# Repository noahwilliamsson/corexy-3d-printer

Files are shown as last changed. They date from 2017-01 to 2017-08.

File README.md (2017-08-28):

# Overview

This is my attempt at designing a 3D printer with [CoreXY](http://corexy.com/theory.html) motion.  There's nothing novel about it except all plastic parts were designed in the open source [OpenSCAD](http://www.openscad.org).  So far it has successfully printed a 20mm calibration cube.

The printer has been built around some 2020 aluminium extrusions I had lying around:

- 4x 500mm beams for the frame (X)
- 4x 420mm beams for the frame (Y)
- 4x 360mm beams for the frame (Z)
- 2x 360mm beams for the bed (X)
- 2x 420mm beams for the bed (Y)

For the linear motion, 4x 12x400mm stainless steel rods (X and Y) and 4x 10x400mm (Z axises) have been used together with 8x LM12UU bearings and IGUS DryLin RJMP-01-10 bearings.

The plastic parts were printed in PLA, with some of the load bearing parts printed at 100% infill.

In the current design it requires 4 NEMA17 stepper motors (two for the corexy motion and two to support the bed in the Z direction).

For the extruder and hotend, an [E3D Titan Extruder](https://e3d-online.com/Titan-Extruder) is used with an [E3D v6 HotEnd](https://e3d-online.com/E3D-v6/Full-Kit/v6-1.75mm-Universal).

Electronics wise, it uses an Arduino Mega2560 r3 board and has been tested with both:

- 4x [Big Easy Driver](http://www.schmalzhaus.com/BigEasyDriver/) stepper motor drivers and a custom board with MOSFETs and misc support electronics
- A standard [RAMPS v1.4](http://reprap.org/wiki/RAMPS_1.4) board

The Arduino board runs the [Marlin 1.1.0 RC8](https://github.com/MarlinFirmware/Marlin) firmware with the following settings in `Configuration.h`:

	#define COREXY
	// Travel limits after homing (units are in mm)
	#define X_MAX_POS 290
	#define Y_MAX_POS 275
	#define Z_MAX_POS 205

The Y max value is no longer up-to-date because it was determined when I was using a cantilever design for the bed (single Z axis).  Unfortunately, it wasn't rigid enough and I got some 5mm flex at the far end.  I've since moved on to a dual Z-axis design to support the bed in two places (not reflected in the .scad file).

This is work in progress but here's a quick screenshot from OpenSCAD of the general idea (not all parts are shown).

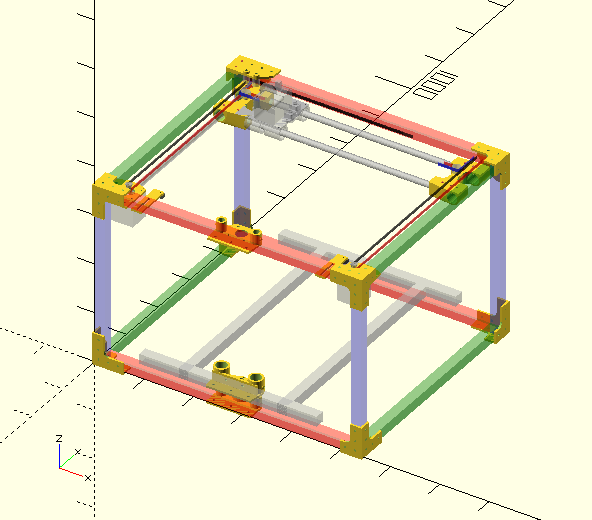
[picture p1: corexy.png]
corexy.scad


# Update 2017

Changed made since the initial commit:

- The horizontal X carriage offered stability but hid the print head so I've opted for a vertical X axis with a new X carriage and new X/Y guide brackets
- The new V2 X carriage is now slightly more modular to make it easier to swap out the print head
- The new V2 X/Y guide brackets are however painful to print properly (use a brim)
- Some parts got slightly rounded corners instead of sharp edges to avoid warping issues
- The X beam length has been reduced to reduce weight of the X axis
- Flexible couplers on the Z axis were replaced with non-flexible ones to reduce lag/flex in the Z axis
- The NEMA17 defs was changed from 43.2mm to 42.3mm (required a re-print of most of the top parts)
- The single, large .scad file has been split up to multiple files

## Imported models

The following STLs were found and downloaded from the internet.

- [BLTouch_extracted.stl](https://www.thingiverse.com/thing:1229934/apps) (CC-BY license)
- [E3D_Titan.stl](https://www.youmagine.com/designs/e3d-titan-extruder-model) (CC-BY-SA license)
- [E3D_V6_1.75mm_Universal_HotEnd_Mockup.stl](https://www.thingiverse.com/thing:341689) (CC-BY license)

# Approximate BOM

Notes:

- All-in-all it's about €1K not including time spent building, waiting, printing and debugging
- Don't cheap out on the hotend, extruder or the heated bed
- While PEI on a heated bed is nice, both PLA and PETG is painless to print on a 4mm float glass bed with 3M Blue Painter's tape (`#2090`)
- Motedis or McMaster-Carr has aluminium beams, steel rods, nuts, washers and bolts for the frame
- China (eBay) has cheaper kits with Arduino+RAMPS 1.4+stepper drivers (€30 in total, saving €50+ vs. buying from E3D)
- The Panucatt Devices _Re-ARM for RAMPS_ board (runs Smoothieware instead of Marlin) is a nice alternative to the Arduino Mega2560 (€40 + shipping)
- I've found the Panucatt Devices _SD6128 Stepper driver_ better able to drive the recent pancake stepper motor E3D offers with their Titan Extruder
- Bearings, misc nuts, washers and bolts can be found on eBay
- Large washers are preferred to spread out the load on plastic parts
- M4 bolts are used around the frame (approx. 150 bolts, washers and alu beam nuts)
- M3 bolts are used in brackets for steppers, electronics, bed leveling and the print head

| Item | Vendor | Count | Price  | Total EUR |
|---|---|---|---|---|
| [Arduino Mega 2560 Compatible Controller Board & USB Cable](https://e3d-online.com/Electrical/Electronics-Boards/Arduino-Mega-2560-Compatible-Board) | E3D Online | 1 | £25 | 28.50 |
| [RAMPS 1.4 - Arduino Mega Pololu Shield](https://e3d-online.com/Electrical/Electronics-Boards/RAMPS-1.4-Arduino-Mega-Pololu-Shield) | E3D Online | 1 | £25 | 28.50 |
| [A4988 Stepper Driver with Heatsink](https://e3d-online.com/A4988-Stepper-Driver-with-Heatsink) | E3D Online | 4 | £6.50  | 29.50 |
| [v6 HotEnd Full Kit - 1.75mm Universal (Direct) (12v)](http://e3d-online.com/E3D-v6/Full-Kit/v6-1.75mm-Universal) (assembled +£12.50) | E3D Online | 1 | £43 | 49.00 |
| [Titan Extruder](https://e3d-online.com/Titan-Extruder)+Mounting bracket+Motor: NEMA17 21N | E3D Online | 1 | £56 | 63.50 |
| [PCB Heated Bed MK2B 12v and 24v](https://e3d-online.com/Mechanical/Print-Surfaces/PCB-Heated-Bed-MK2B-12v-and-24v) | E3D Online | 1 | £12.50 | 13.50 |
| [Borosilicate Glass Beds 214x214x4](https://e3d-online.com/Print-Surfaces/Borosilicate-Bed-200x200) (214x314x4 +£7.00) | E3D Online | 1 | £22 | 25.00 |
| [100k Ohm NTC Thermistor - Semitec](https://e3d-online.com/Electrical/100k-Ohm-NTC-Thermistor-Semitec) | E3D Online | 1 | £3.50  | 4.00 |
| [NEMA17 47N-cm - High Torque Axes Stepper Motor - Wantai](https://e3d-online.com/Electrical/Stepper-Motors/NEMA17-47Ncm) | E3D Online | 4 | £9.30  | 42.00 |
| [GT2 Belt (6mm) (per 100mm)](https://e3d-online.com/Mechanical/Motion/GT2-Belt-6mm) | E3D Online | 24 | £0.35  | 9.50 |
| [GT2 Pulley (16 tooth)](https://e3d-online.com/Mechanical/Motion/GT2-Pulley-16-Tooth) | E3D Online | 2 | £3.50  | 8.00 |
| [Flexible motor coupling 5mm to 8mm](https://e3d-online.com/Mechanical/Motion/Flexible-motor-coupling-5mm-to-8mm) | E3D Online | 2 | £2.50  | 5.65 |
| [40x40x10mm 12v DC Fan](https://e3d-online.com/Electrical/Fans/40x40x10mm-12v-DC-Fan) | E3D Online | 2 | £4.50  | 10.50 |
| [Bulldog Clips x 4](https://e3d-online.com/Mechanical/Fixings/Bulldog%20Clips) | E3D Online | 1 | £0.90  | 1.00 |
| [Compression spring - 20mm x 7.5mm](https://e3d-online.com/Mechanical/Fixings/Compression-spring-20mmx7.5mm-) | E3D Online | 4 | £0.50  | 2.50 |
| [Endstop Microswitches - Omron](https://e3d-online.com/Endstop-Microswitches-Omron) | E3D Online | 5 | £1.50  | 8.50 |
| E3D shipping and VAT (£16+£61) | | 1 | £77 | 87.00 |
| E3D Total | | 1 | £367 | 415.00 |
| | | | | |
| Be Quiet! ATX PSU | | 1 | €60 | 60.00 |
| Filament 1.75mm 1KG spool | | 1 | €30 | 30.00 |
| 8x400mm T8 2mm pitch lead screw plus nut | | 2 | €10 | 20.00 |
| NEMA17 stepper motor vibration dampener | | 2 | €2.5 | 5.00 |
| Misc electrical cables and cable guides | | 1 | €40 | 40.00 |
| Aluminium beams 20x20 (X 4x500mm; Y 6x420mm; Z 6x360mm) | | 1 | €100 | 100.00 |
| Nuts and bolts | | 1 | €150 | 150.00 |
| Stainless steel rods 12x400mm (X and Y guides) | | 4 | €8 | 32.00 |
| Stainless steel rods 8x3600mm (Z guides) | | 4 | €7 | 28.00 |
| Bearing 608 (Z screw bottom) | | 2 | €3 | 6.00 |
| Bearing F624 (X/Y guide bracket) | | 8 | €3 | 24.00 |
| Bearing F695 (corner brackets) | | 16 | €3 | 18.00 |
| Bearing LM12UU (X/Y guide rods) | | 8 | €4 | 32.00 |
| Bearing LM8UU (Z guide rods) | | 4 | €4 | 16.00 |
| Printed parts | | 1 | €50 | 50.00 |
| | | | | |
| Total | | 1 | €1030  | 1030.00 |

# Wiring

RAMPS 1.4 pinout
RAMPS 1.4 wiring

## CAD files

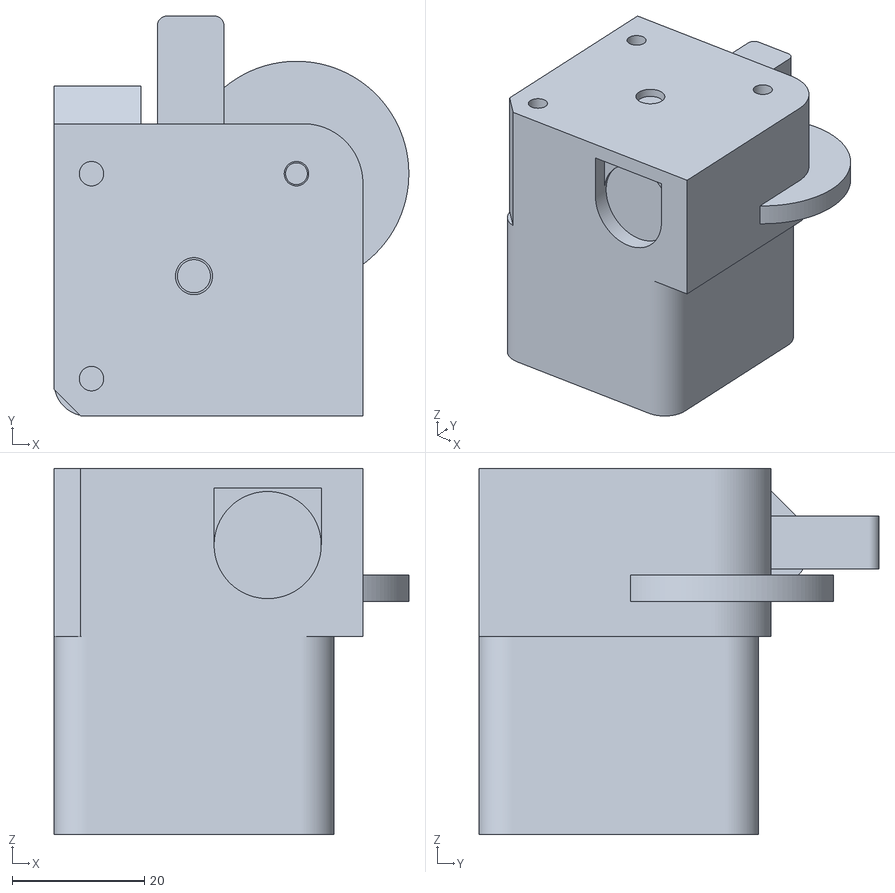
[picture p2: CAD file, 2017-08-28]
E3D_Titan.stl
53.7 x 60.5 x 55.4

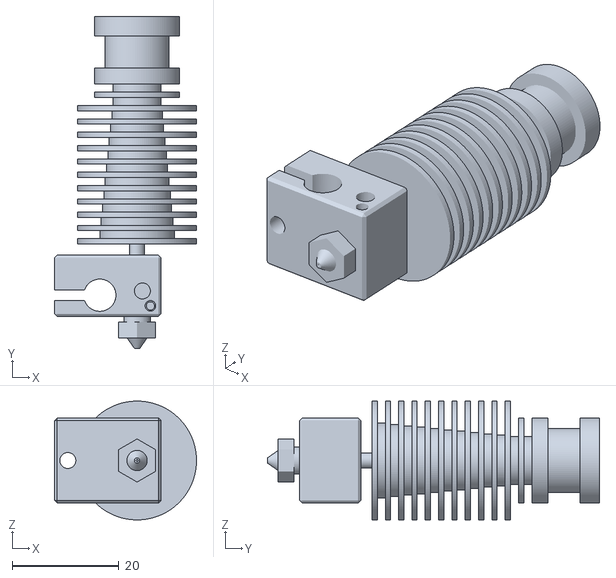
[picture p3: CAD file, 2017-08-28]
E3D_V6_1.75mm_Universal_HotEnd_Mockup.stl
26.6 x 62.3 x 22.3

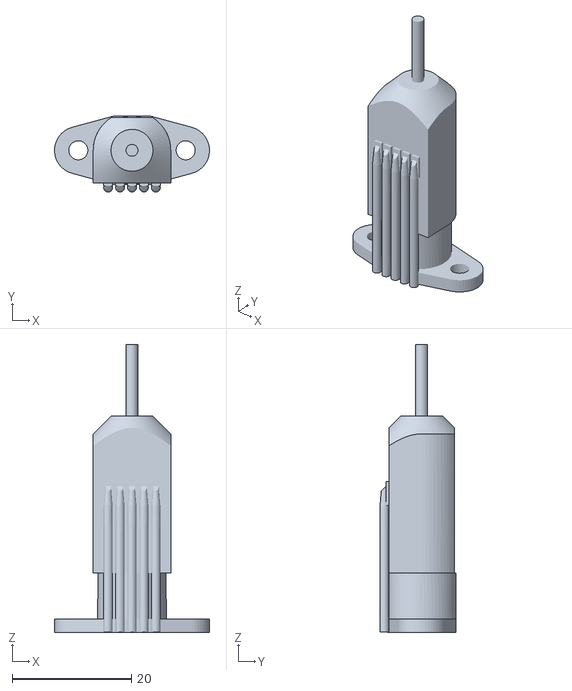
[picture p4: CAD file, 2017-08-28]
BLTouch_extracted.stl
26.0 x 12.8 x 48.3

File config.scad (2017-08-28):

/**
 * CoreXY v2
 * Configuration parameters
 *
 *   -- noah@hack.se, 2016-2017
 */

// Sizes for bearing, screw holes/taps, ..
include <defs.scad>


// Wall thickness
thickness=4;
// Aluminium extrusion size
beamSize=20;

xBeamLength=500;
xRodLength=400;
xBearing=lm12uu;
// XXX: New
xRodLength=400;
xBeamLength=420;
xBearing=lm10uu;

yBeamLength=420;
yRodLength=400;
yBearing=lm10luu;

zBeamLength=360;
zRodLength=300;
zBearing=lm8uu;  // Guide rod
zLeadScrewBearing=B608;
zNut=[8,22,10.5, 8]; // ID, OD (flange), OD (cylinder), mounting hole center-to-center radius

// Bed beams
bedXBeamLength=360;
bedYBeamLength=420;


// Bearings for belt on xy guide bracket
//xyBearing=F625; // 2016
xyBearing=F695; // update 2017
// XY guide bracket clearance from beams
beamClearance=.5;
// Y rod offset from beam, should be > (yBearing[1]/2+thickness)
yRodBeamOffset=13;

// Corner bearings
cornerBearing=F695;

// Distance between X rods (center-to-center)
// Lulzbot, Adapto and other designs use 70mm distances
xRodDistance=70;
// How much to shift X axis up
xRodZShift=5;
// Total width of X rod bracket that is sliding on the Y axis
// Should be at least xRodDistance+2*(xBearing[1]/2+thickness)
xyGuideBracketWidth=99;

xyStepper=NEMA17;
zStepper=NEMA17;
xyPulleySize=9.6;
xyPulleySizeWithBelt=11.6;
xyBeltThickness=1;

xCarriageWidth=70;
xCarriageHeight=xRodDistance+xBearing[1];
xRodMinimumXOffset=beamSize+yRodBeamOffset+yBearing[1]/2;
xRodCalculatedXOffset = beamSize+(xBeamLength-xRodLength)/2;
xGuideLengths=xRodCalculatedXOffset-xRodMinimumXOffset+10+thickness;
xTravel=beamSize+xBeamLength+beamSize-2*(xRodMinimumXOffset+xGuideLengths)-xCarriageWidth;
echo("INFO:",xTravel=xTravel, xRodMinimumXOffset=xRodMinimumXOffset, xRodCalculatedXOffset=xRodCalculatedXOffset, xGuideLengths=xGuideLengths);

yBearingShellDiameter = yBearing[1]+2*thickness < 2*(yRodBeamOffset-beamClearance)? yBearing[1]+2*thickness: 2*(yRodBeamOffset-beamClearance);
echo("Y bearing shell diameter", yBearing[1]+2*thickness, "can be at most", 2*(yRodBeamOffset-beamClearance),"with yRodBeamOffset",yRodBeamOffset,"and beamClearance",beamClearance);

if(yRodBeamOffset <= (yBearing[1]/2+thickness))
    echo("WARNING: yRodBeamOffset too small, need to be at least", (yBearing[1]/2+thickness));
if(xyGuideBracketWidth < xRodDistance+2*(xBearing[1]/2+thickness))
    echo("WARNING: xyGuideBracketWidth too small, need to be at least", xRodDistance+2*(xBearing[1]/2+thickness));


// For the Arduino bracket
board = ArduinoMega2560_Board;
holes = ArduinoMega2560_ReverseHoles;
standoffHeight = 3;

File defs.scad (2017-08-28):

/**
 * CoreXY v2 config
 *
 *   -- noah@hack.se, 2016-2017
 */


/**
 * @section Definitions
 */
// inner diameter, outer diameter, length/height
lm8uu=[8,15,24];    // same as RJ4JP-01-08
lm8luu=[8,15,45];
rjmp0108=[8,16,25]; // RJMP-01-08

lm10uu=[10,19,29];  // same as RJ4JP-01-10
lm10luu=[10,19,55];
rjmp0110=[10,19,29]; // RJMP-01-10

lm12uu=[12,21,30];  // same as  -01-12
lm12luu=[12,21,57];
rjmp0112=[12,22,32]; // RJMP-01-12

// Ball bearings (ID, OD (not considering flange), thickness, flange thickness)
B623=[3,10,5];
B624=[4,13,5];
F624=[4,13,5, 1];
B625=[5,16,5];
F625=[5,16,5, 1];
F695=[5,13,4, 1];
B626=[6,19,6];
B608=[8,22,7];

/**
 * @section Hole configuration
 */
M2tap=1.85;
M3tap=2.85;
M3hole=3.6;
M4tap=3.9;
M4hole=4.6;
M5tap=4.8;
M5hole=5.4;
M5nut=8;
M8tap=7.5;

// X, Y, Height, axle diameter, half distance between two mounting holes, axle length
// Was: NEMA17=[43.2, 43.2, 50, 5, 31/2, 22];
NEMA17=[42.3, 42.3, 50, 5, 31/2, 22];


/**
 * @section Electronics definitions
 */

// https://blog.arduino.cc/2011/01/05/nice-drawings-of-the-arduino-uno-and-mega-2560/
ArduinoMega2560_Board=[101.6,53.4]; // X, Y
ArduinoMega2560_Holes=[
        [14, 2.54],  // bottom left
        [15.24, 50.8], // top left
//        [66.04, 7.62],  // bottom middle,
//        [66.04, 35.56],  // top middle,
        [96.52, 2.54],  // bottom right,
        [90.17, 50.8],  // top right,
];
ArduinoMega2560_ReverseHoles = [
    [11.43, 2.54],
    [86.36, 2.54],
//    [35.56, 17.78],
//    [35.56, 45.72],
    [5.08, 50.8],
    [87.63, 50.8]
];

Pi3_Board=[85,56];
Pi3_Holes=[
    [3.5, 3.5],
    [3.5, 52.5],
    [61.5, 52.5],
    [61.5, 3.5]
];

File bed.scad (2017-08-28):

/**
 * CoreXY v2
 * Modules for the bed
 *
 *   -- noah@hack.se, 2016-2017
 */

// Sizes for bearing, screw holes/taps, ..
include <defs.scad>
// Printer configuration
include <config.scad>

// Modules
use <helpers.scad>


// Print statements
*!bedGripThing();
*!printBedCorners();
*!printBedDistances();

// Print helpers
module printBedCorners() {
    translate([0,0,0]) bedCorner();
    translate([42,0,0]) bedCorner();
    translate([0,42,0]) bedCorner();
    translate([42,42,0]) bedCorner();
}
module printBedDistances() {
    translate([0,0,0]) bedDistance();
    translate([42,0,0]) bedDistance();
    translate([0,42,0]) bedDistance();
    translate([42,42,0]) bedDistance();
}

// To squeeze a plate of 4mm float glass and 4mm cork against a 2020 alu beam
module bedGripThing() {
    distance=28;
    thickness=4;
    difference() {
        union() {
            hull() for(x=[-1,1],y=[-1,1],z=[-1,1])
                translate([(thickness)/2+x*(distance)/2,
                            (2*thickness+distance/2)+y*(2*thickness+distance)/2,
                            5+5*z])
                    sphere(d=1,$fn=6);
        }
        translate([-2*thickness,2*thickness,-.5]) hull() for(x=[-1,1],y=[-1,1],z=[-1,1])
            translate([distance/2+x*distance/2, distance/2+y*distance/2, 5+(5+1)*z])
                sphere(d=1,$fn=6);
    }
}

// Bed leveling screw bracket for Z gantry
module bedCorner() {
    difference() {
        union() {
            cube([beamSize, 6*beamSize/7, thickness]);
            translate([0,5*beamSize/7,0]) cube([beamSize, 4*beamSize/7, thickness]);
            translate([beamSize/4,5*beamSize/7,0]) cube([beamSize/2, 4*beamSize/7, thickness*2]);
            translate([3*beamSize/4, 3*beamSize/3,8]) rotate([0,-90,0]) cylinder(d=12, h=beamSize/2);
        }
        // Mounting holes
        translate([beamSize/2, 2*beamSize/5, -.5]) polyhole(d=M4hole,h=thickness*2+1);
        translate([beamSize+.5, 3*beamSize/3,8]) rotate([0,-90,0]) cylinder(d=M3tap, h=beamSize+1);
    }
}

// Thing for the angled corners on the borosillicate glass
module bedDistance() {
    difference() {
        union() {
            cylinder(d=8,h=thickness);
            rotate(45) translate([-4,-6,0]) cube([8,12,thickness]);
        }
        translate([0,0,-.5]) cylinder(d=M3hole, h=thickness+1);
    }
}

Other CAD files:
corexy-v2.scad
corexy.scad
display.scad
electronics.scad
frame.scad
helpers.scad
xAxis.scad
xyShared.scad
yAxis.scad
zAxis.scad

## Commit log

2017-01-15 Initial import
    [corexy.scad]
2017-08-28 Vertical X axis for V2, approx. BOM, split up scad (WIP)
    [BLTouch_extracted.stl, E3D_Titan.stl, E3D_V6_1.75mm_Universal_HotEnd_Mockup.stl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]
